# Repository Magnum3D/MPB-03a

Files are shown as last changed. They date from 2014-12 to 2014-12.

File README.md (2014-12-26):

MPB-03a
===========
Reprap Electronics for Magnum printers based on Printrboard

Отличия платы:

1. Плата питается напряжением 24 вольта (стол, экструдер и двигатели)
2. Установлен ЦАП для регулировки тока двигателей командами G-кода (как в версии F и исправлены ошибки).
3. Для питания вентиляторов добавлен дополнительный импульсный преобразователь на 12 вольт
4. Добавлено 4 мосфета с обвязкой - 2 для вентиляторов и 2 для светодиодных лент.
5. Заменены разъемы питания и нагревательного стола на мощные разъемы Molex.
6. Добавлен внешний разъем DSUB и на него выведено питание, ножки процессора и шина I2C
7. Мелкие исправления, доработки.

Постоянно ведется работа над усовершенствованием и доработкой платы, поэтому версия установленная в конкретный эксземпляр принтера может незначительно отличаться.

For more info see the Reprap wiki page http://reprap.org/wiki/Printrboard

The BoM with Digikey P/N's is available here: http://goo.gl/hQNEm

This project, and all of its design files (including the layout), is licensed under the [Creative Commons Attribution-ShareAlike 3.0 Unported](http://creativecommons.org/licenses/by-sa/3.0/) license.

Anyone found to be in violation of this license may not produce or discribute any products using these designs, and will have legal action taken against them.

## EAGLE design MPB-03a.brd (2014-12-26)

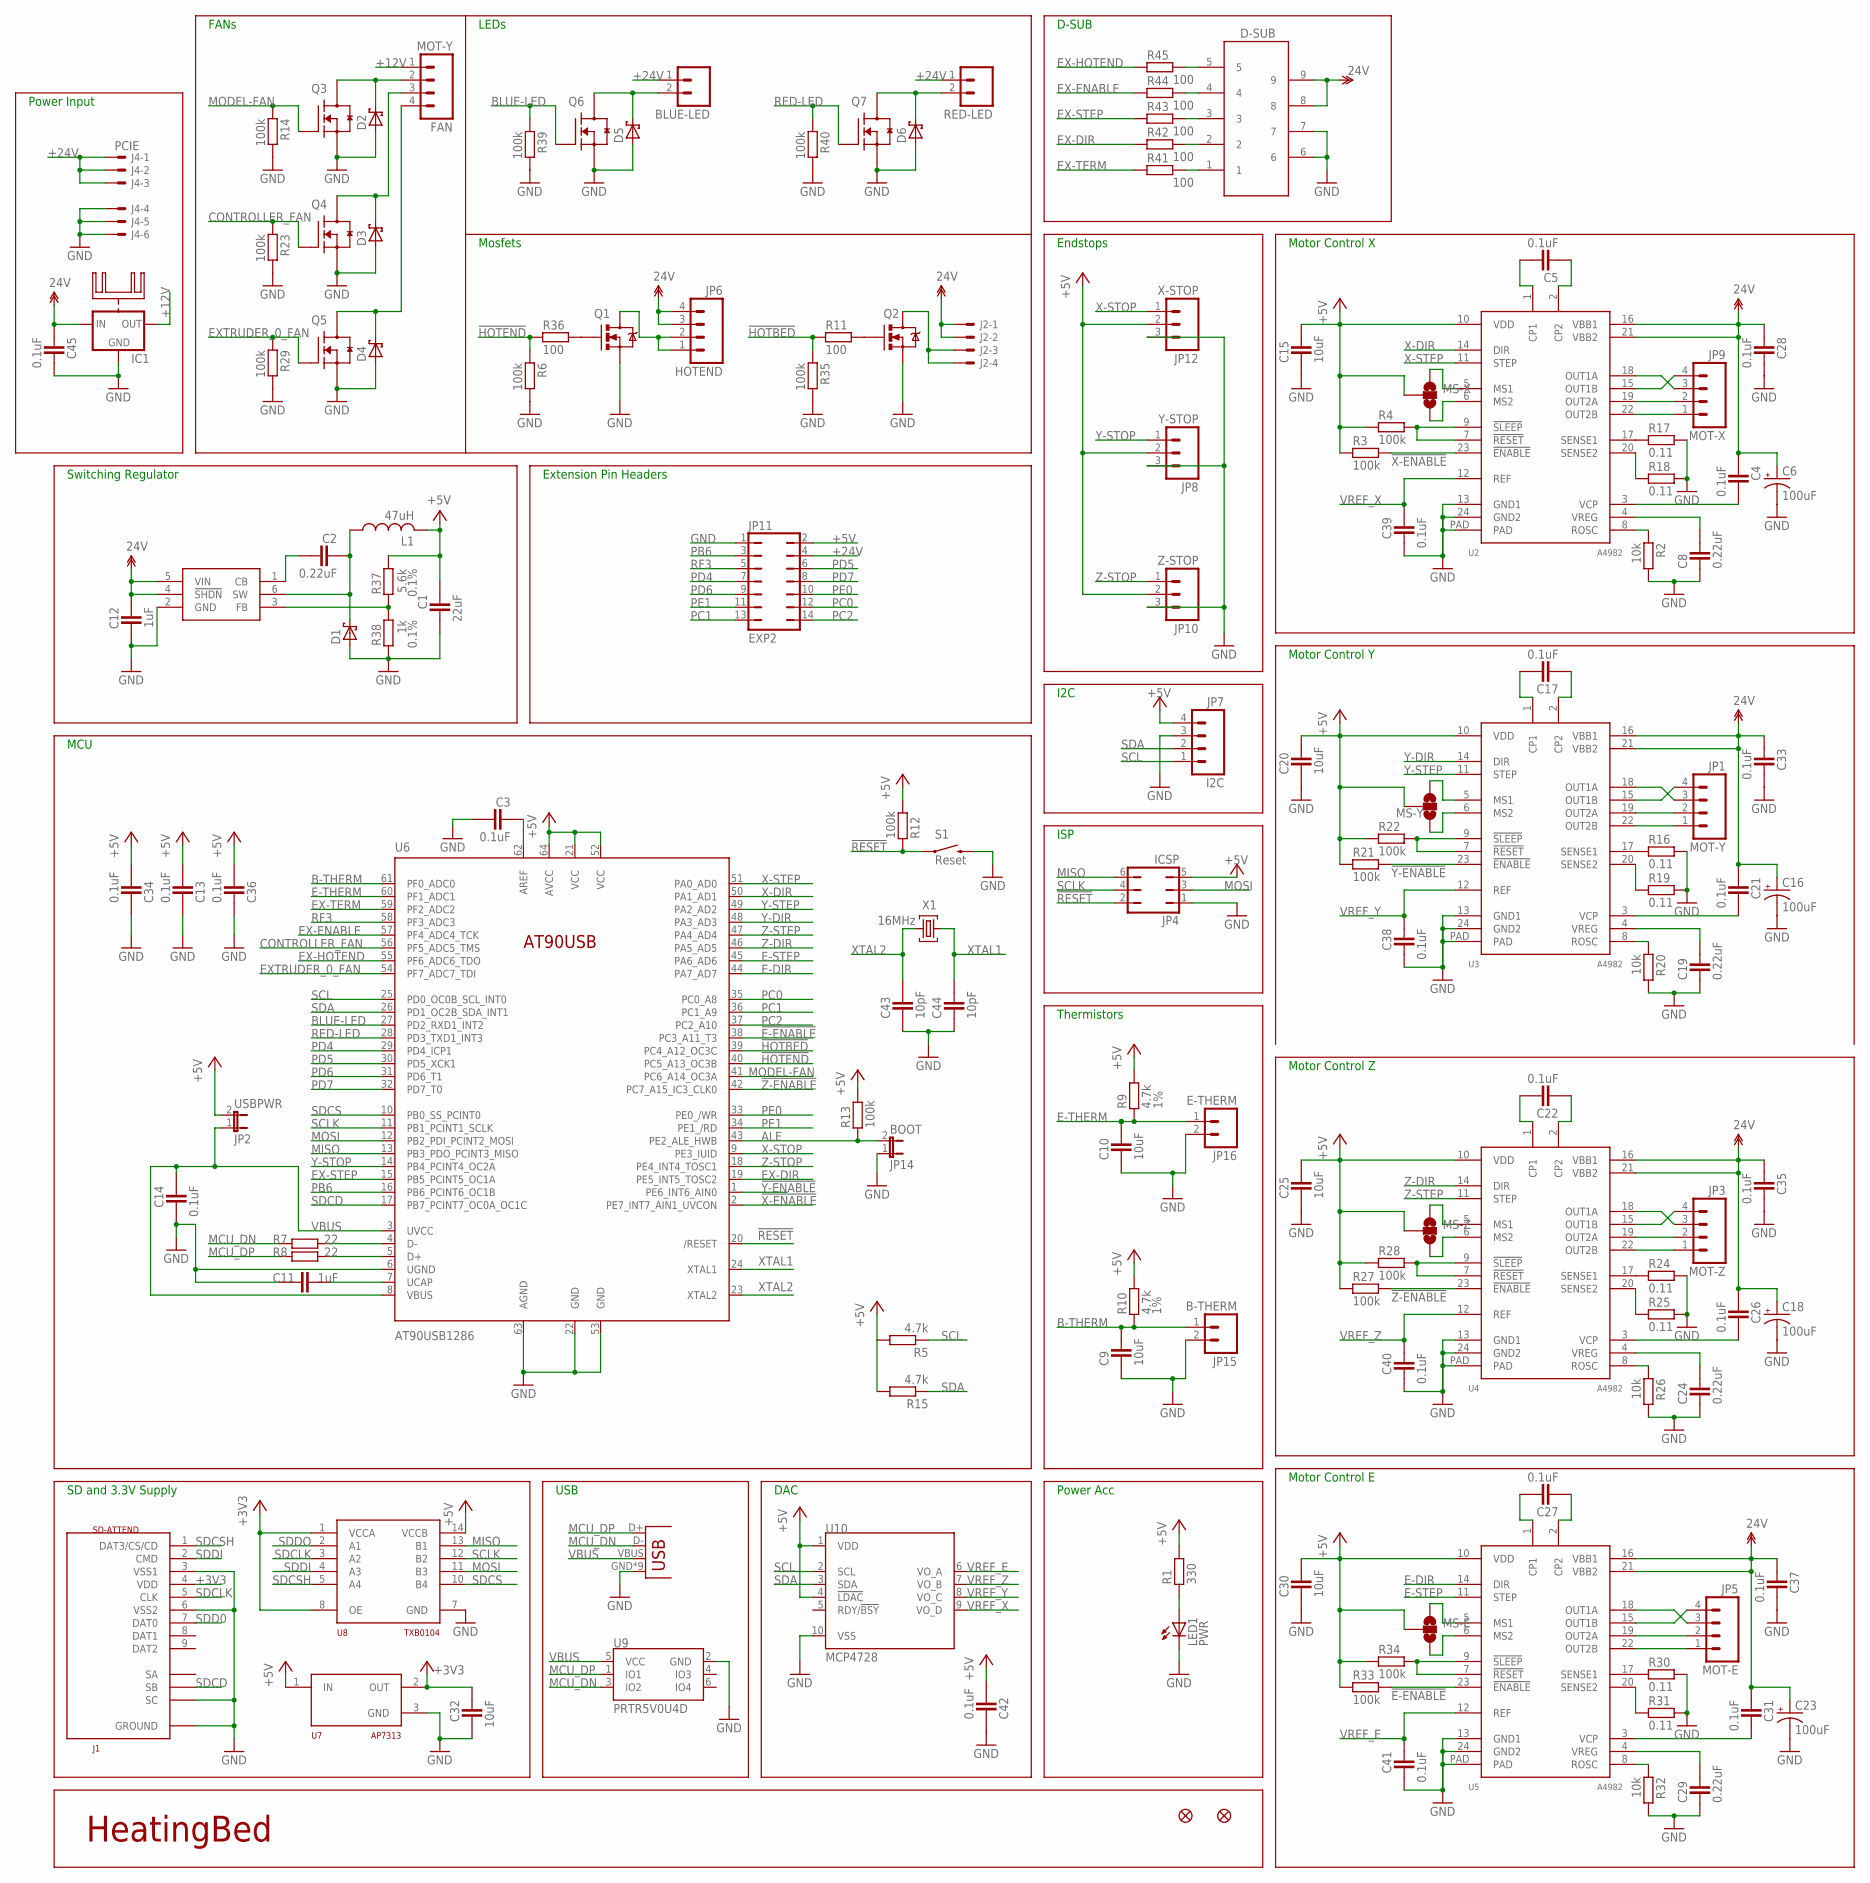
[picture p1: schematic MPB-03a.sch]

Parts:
BLUE-LED: M02POLAR; MOLEX-1X2
C1: 22uF; CAPC2012X145AN
C2, C8, C19, C24, C29: 0.22uF; CAPC2012X145AN
C3, C4, C5, C13, C14, C17, C21, C22, C26, C27, C28, C31, C33, C34, C35, C36, C37, C38, C39, C40, C41, C42, C45: 0.1uF; CAPC2012X145AN
C6, C16, C18, C23: 100uF; PANASONIC_D
C9, C10, C15, C20, C25, C30, C32: 10uF; CAPC2012X145AN
C11, C12: 1uF; CAPC2012X145AN
C43, C44: 10pF; CAPC2012X145AN
D1, D2, D3, D4, D5, D6: SCH-DIODESMA; SMA
D-SUB: 618009211721
FAN: MOT-Y; MOLEX-1X4
IC1: 78XXH; TO220-15X17X25
J1: SD-ATTEND
J2: 5566-4
J3: USB-MICRO-PTH; USB-MICROB-PTH
J4: PCIE; 5566-6
JP1: MOT-Y; MOLEX-1X4
JP2: USBPWR; 1X02
JP3: MOT-Z; MOLEX-1X4
JP4: ICSP; JP3Q
JP5: MOT-E; MOLEX-1X4
JP6: HOTEND; MOLEX-1X4
JP7: I2C; MOLEX-1X4
JP8: Y-STOP; MOLEX-1X3
JP9: MOT-X; MOLEX-1X4
JP10: Z-STOP; MOLEX-1X3
JP11: EXP2; JP7Q
JP12: X-STOP; MOLEX-1X3
JP14: BOOT; 1X02
JP15: B-THERM; 1X02
JP16: E-THERM; 1X02
JP26, JP33: FIDUCIAL1X2.5; FIDUCIAL-1X2.5
L1: 47uH; SDR1006
LED1: PWR; CHIP-LED0805
MS-E: SOLDERJUMPER_2WAYCONNECTED; SJ_3_CONNECTED
MS-X: SOLDERJUMPER_2WAYCONNECTED; SJ_3_CONNECTED
MS-Y: SOLDERJUMPER_2WAYCONNECTED; SJ_3_CONNECTED
MS-Z: SOLDERJUMPER_2WAYCONNECTED; SJ_3_CONNECTED
Q1, Q2: RFP30N06LE; TO220V
Q3, Q4, Q5, Q6, Q7: RFP30N06LE; SOT95P280X135-3N
R1: 330; RESC2012X70N
R2, R20, R26, R32: 10k; RESC2012X70N
R3, R4, R6, R12, R13, R14, R21, R22, R23, R27, R28, R29, R33, R34, R35, R39, R40: 100k; RESC2012X70N
R5, R15: 4.7k; RESC2012X70N
R7, R8: 22; RESC2012X70N
R9, R10: 4.7k; RESC2012X70N; TOLERANCE 1%
R11, R36, R41, R42, R43, R44, R45: 100; RESC2012X70N
R16, R17, R18, R19, R24, R25, R30, R31: 0.11; RESC2012X70N
R37: 5.6k; RESC2012X70N; TOLERANCE 0.1%
R38: 1k; RESC2012X70N; TOLERANCE 0.1%
RED-LED: M02POLAR; MOLEX-1X2
S1: Reset; TACTILE_SWITCH_TALL
U1: LM2841; TSOT6
U2, U3, U4, U5: A4982; TSSOP-24
U6: AT90USB1286; TQFP64-2
U7: AP7313; SOT23C
U8: TXB0104; TSSOP14
U9: PRTR5V0U4D; SOT23-6
U10: MCP4728; MSOP10
X1: 16MHz; NDK-XTAL

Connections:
!E-ENABLE: R33.2, U5.23 (!ENABLE), U6.38 (PC3_A11_T3)
!HOTBED: R11.1, R35.1, U6.39 (PC4_A12_OC3C)
!HOTEND: R6.1, R36.1, U6.40 (PC5_A13_OC3B)
!RESET: JP4.2, R12.1, S1.A2 (1), U6.20 (/RESET)
!X-ENABLE: R3.2, U2.23 (!ENABLE), U6.2 (PE7_INT7_AIN1_UVCON)
!Y-ENABLE: R21.2, U3.23 (!ENABLE), U6.1 (PE6_INT6_AIN0)
!Z-ENABLE: R27.2, U4.23 (!ENABLE), U6.42 (PC7_A15_IC3_CLK0)
+3V3: C32.1, J1.4 (VDD), U7.2 (OUT), U8.1 (VCCA), U8.8 (OE)
+5V: C1.1, C13.2, C15.2, C20.2, C25.2, C30.2, C34.2, C36.2, C42.2, JP2.2, JP4.5, JP7.4, JP8.2, JP10.2, JP11.2, JP12.2, L1.P$2 (2), MS-E.2, MS-X.2, MS-Y.2, MS-Z.2, R1.2, R3.1, R4.1, R5.2, R9.2, R10.2, R12.2, R13.2, R15.2, R21.1, R22.1, R27.1, R28.1, R33.1, R34.1, R37.1, U2.10 (VDD), U3.10 (VDD), U4.10 (VDD), U5.10 (VDD), U6.21 (VCC), U6.52 (VCC), U6.64 (AVCC), U7.1 (IN), U8.14 (VCCB), U10.1 (VDD), U10.4 (!LDAC)
+12V: FAN.1, IC1.OUT
+24V: BLUE-LED.1, C4.1, C6.+, C12.1, C16.+, C18.+, C21.1, C23.+, C26.1, C28.1, C31.1, C33.1, C35.1, C37.1, C45.1, D-SUB.8, D-SUB.9, IC1.IN, J2.1, J2.2, J4.1, J4.2, J4.3, JP6.3, JP6.4, JP11.4, RED-LED.1, U1.4 (!SHDN), U1.5 (VIN), U2.16 (VBB1), U2.21 (VBB2), U3.16 (VBB1), U3.21 (VBB2), U4.16 (VBB1), U4.21 (VBB2), U5.16 (VBB1), U5.21 (VBB2)
ALE: JP14.2, R13.1, U6.43 (PE2_ALE_HWB)
AREF: C3.1, U6.62 (AREF)
B-THERM: C9.2, JP15.1, R10.1, U6.61 (PF0_ADC0)
BLUE-LED: Q6.1 (G), R39.1, U6.27 (PD2_RXD1_INT2)
CONTROLLER_FAN: Q4.1 (G), R23.1, U6.56 (PF5_ADC5_TMS)
E-DIR: U5.14 (DIR), U6.44 (PA7_AD7)
E-STEP: U5.11 (STEP), U6.45 (PA6_AD6)
E-THERM: C10.2, JP16.1, R9.1, U6.60 (PF1_ADC1)
EX-DIR: R42.1, U6.19 (PE5_INT5_TOSC2)
EX-ENABLE: R44.1, U6.57 (PF4_ADC4_TCK)
EX-HOTEND: R45.1, U6.55 (PF6_ADC6_TDO)
EX-STEP: R43.1, U6.15 (PB5_PCINT5_OC1A)
EX-TERM: R41.1, U6.59 (PF2_ADC2)
EXTRUDER_0_FAN: Q5.1 (G), R29.1, U6.54 (PF7_ADC7_TDI)
GND: C1.2, C3.2, C6.-, C8.1, C9.1, C10.1, C11.1, C12.2, C13.1, C14.2, C15.1, C16.-, C18.-, C19.1, C20.1, C23.-, C24.1, C25.1, C28.2, C29.1, C30.1, C32.2, C33.2, C34.1, C35.2, C36.1, C37.2, C38.2, C39.2, C40.2, C41.2, C42.1, C43.1, C44.1, C45.2, D1.A, D2.A, D3.A, D4.A, D5.A, D6.A, D-SUB.6, D-SUB.7, IC1.GND, J1.3 (VSS1), J1.6 (VSS2), J1.G (GROUND), J1.SC, J3.GND, J3.GND1 (GND), J3.GND2 (GND), J3.GND3 (GND), J3.GND4 (GND), J3.GND5 (GND), J3.GND6 (GND), J3.GND7 (GND), J3.GND8 (GND), J4.4, J4.5, J4.6, JP4.1, JP7.3, JP8.3, JP10.3, JP11.1, JP12.3, JP14.1, JP15.2, JP16.2, LED1.C, Q1.3 (S), Q2.3 (S), Q3.2 (S), Q4.2 (S), Q5.2 (S), Q6.2 (S), Q7.2 (S), R2.2, R6.2, R14.2, R16.2, R17.2, R18.2, R19.2, R20.2, R23.2, R24.2, R25.2, R26.2, R29.2, R30.2, R31.2, R32.2, R35.2, R38.2, R39.2, R40.2, S1.B2 (2), U1.2 (GND), U2.13 (GND1), U2.24 (GND2), U2.PAD, U3.13 (GND1), U3.24 (GND2), U3.PAD, U4.13 (GND1), U4.24 (GND2), U4.PAD, U5.13 (GND1), U5.24 (GND2), U5.PAD, U6.6 (UGND), U6.22 (GND), U6.53 (GND), U6.63 (AGND), U7.3 (GND), U8.7 (GND), U9.2 (GND), U10.10 (VSS)
HOTBED-GND: J2.3, J2.4, Q2.2 (D)
HOTEND-GND: JP6.1, JP6.2, Q1.2 (D)
MCU_DN: J3.D-, R7.1, U9.3 (IO2)
MCU_DP: J3.D+, R8.1, U9.1 (IO1)
MISO: JP4.6, U6.13 (PB3_PDO_PCINT3_MISO), U8.13 (B1)
MODEL-FAN: Q3.1 (G), R14.1, U6.41 (PC6_A14_OC3A)
MOSI: JP4.3, U6.12 (PB2_PDI_PCINT2_MOSI), U8.11 (B3)
unnamed: LED1.A, R1.1
unnamed: D2.C, FAN.2, Q3.3 (D)
unnamed: R7.2, U6.4 (D-)
unnamed: R8.2, U6.5 (D+)
unnamed: D3.C, FAN.3, Q4.3 (D)
unnamed: D4.C, FAN.4, Q5.3 (D)
unnamed: Q2.1 (G), R11.2
unnamed: BLUE-LED.2, D5.C, Q6.3 (D)
unnamed: C11.2, U6.7 (UCAP)
unnamed: JP9.3, U2.18 (OUT1A)
unnamed: C5.2, U2.1 (CP1)
unnamed: C5.1, U2.2 (CP2)
unnamed: R2.1, U2.8 (ROSC)
unnamed: R17.1, U2.17 (SENSE1)
unnamed: R18.1, U2.20 (SENSE2)
unnamed: C4.2, U2.3 (VCP)
unnamed: JP9.4, U2.15 (OUT1B)
unnamed: D-SUB.5, R45.2
unnamed: C8.2, U2.4 (VREG)
unnamed: JP9.2, U2.19 (OUT2A)
unnamed: R4.2, U2.7 (!RESET), U2.9 (!SLEEP)
unnamed: R37.2, R38.1, U1.3 (FB)
unnamed: JP9.1, U2.22 (OUT2B)
unnamed: JP1.2, U3.19 (OUT2A)
unnamed: JP1.1, U3.22 (OUT2B)
unnamed: JP1.4, U3.15 (OUT1B)
unnamed: MS-X.1, U2.5 (MS1)
unnamed: MS-X.3, U2.6 (MS2)
unnamed: C17.2, U3.1 (CP1)
unnamed: C17.1, U3.2 (CP2)
unnamed: JP1.3, U3.18 (OUT1A)
unnamed: R19.1, U3.20 (SENSE2)
unnamed: D6.C, Q7.3 (D), RED-LED.2
unnamed: R20.1, U3.8 (ROSC)
unnamed: C19.2, U3.4 (VREG)
unnamed: R22.2, U3.7 (!RESET), U3.9 (!SLEEP)
unnamed: C21.2, U3.3 (VCP)
unnamed: R16.1, U3.17 (SENSE1)
unnamed: JP3.4, U4.15 (OUT1B)
unnamed: JP3.3, U4.18 (OUT1A)
unnamed: JP3.2, U4.19 (OUT2A)
unnamed: MS-Y.1, U3.5 (MS1)
unnamed: MS-Y.3, U3.6 (MS2)
unnamed: C22.2, U4.1 (CP1)
unnamed: C22.1, U4.2 (CP2)
unnamed: R24.1, U4.17 (SENSE1)
unnamed: R25.1, U4.20 (SENSE2)
unnamed: R26.1, U4.8 (ROSC)
unnamed: C24.2, U4.4 (VREG)
unnamed: R28.2, U4.7 (!RESET), U4.9 (!SLEEP)
unnamed: C26.2, U4.3 (VCP)
unnamed: JP3.1, U4.22 (OUT2B)
unnamed: JP5.4, U5.15 (OUT1B)
unnamed: JP5.3, U5.18 (OUT1A)
unnamed: JP5.2, U5.19 (OUT2A)
unnamed: MS-Z.1, U4.5 (MS1)
unnamed: MS-Z.3, U4.6 (MS2)
unnamed: C27.2, U5.1 (CP1)
unnamed: C27.1, U5.2 (CP2)
unnamed: R30.1, U5.17 (SENSE1)
unnamed: R31.1, U5.20 (SENSE2)
unnamed: D-SUB.4, R44.2
unnamed: R32.1, U5.8 (ROSC)
unnamed: C29.2, U5.4 (VREG)
unnamed: R34.2, U5.7 (!RESET), U5.9 (!SLEEP)
unnamed: C31.2, U5.3 (VCP)
unnamed: JP5.1, U5.22 (OUT2B)
unnamed: D-SUB.3, R43.2
unnamed: D-SUB.2, R42.2
unnamed: Q1.1 (G), R36.2
unnamed: MS-E.1, U5.5 (MS1)
unnamed: MS-E.3, U5.6 (MS2)
unnamed: D-SUB.1, R41.2
unnamed: C2.1, D1.C, L1.P$1 (1), U1.6 (SW)
unnamed: C2.2, U1.1 (CB)
PB6: JP11.3, U6.16 (PB6_PCINT6_OC1B)
PC0: JP11.12, U6.35 (PC0_A8)
PC1: JP11.13, U6.36 (PC1_A9)
PC2: JP11.14, U6.37 (PC2_A10)
PD4: JP11.7, U6.29 (PD4_ICP1)
PD5: JP11.6, U6.30 (PD5_XCK1)
PD6: JP11.9, U6.31 (PD6_T1)
PD7: JP11.8, U6.32 (PD7_T0)
PE0: JP11.10, U6.33 (PE0_/WR)
PE1: JP11.11, U6.34 (PE1_/RD)
RED-LED: Q7.1 (G), R40.1, U6.28 (PD3_TXD1_INT3)
RF3: JP11.5, U6.58 (PF3_ADC3)
SCL: JP7.1, R5.1, U6.25 (PD0_OC0B_SCL_INT0), U10.2 (SCL)
SCLK: JP4.4, U6.11 (PB1_PCINT1_SCLK), U8.12 (B2)
SDA: JP7.2, R15.1, U6.26 (PD1_OC2B_SDA_INT1), U10.3 (SDA)
SDCD: J1.SB, U6.17 (PB7_PCINT7_OC0A_OC1C)
SDCLK: J1.5 (CLK), U8.3 (A2)
SDCS: U6.10 (PB0_SS_PCINT0), U8.10 (B4)
SDCSH: J1.1 (DAT3/CS/CD), U8.5 (A4)
SDD0: J1.7 (DAT0)
SDDI: J1.2 (CMD), U8.4 (A3)
SDDO: U8.2 (A1)
VBUS: C14.1, J3.VBUS, JP2.1, U6.3 (UVCC), U6.8 (VBUS), U9.5 (VCC)
VREF_E: C41.1, U5.12 (REF), U10.6 (VO_A)
VREF_X: C39.1, U2.12 (REF), U10.9 (VO_D)
VREF_Y: C38.1, U3.12 (REF), U10.8 (VO_C)
VREF_Z: C40.1, U4.12 (REF), U10.7 (VO_B)
X-DIR: U2.14 (DIR), U6.50 (PA1_AD1)
X-STEP: U2.11 (STEP), U6.51 (PA0_AD0)
X-STOP: JP12.1, U6.9 (PE3_IUID)
XTAL1: C44.2, U6.24 (XTAL1), X1.P$1 (1)
XTAL2: C43.2, U6.23 (XTAL2), X1.P$2 (2)
Y-DIR: U3.14 (DIR), U6.48 (PA3_AD3)
Y-STEP: U3.11 (STEP), U6.49 (PA2_AD2)
Y-STOP: JP8.1, U6.14 (PB4_PCINT4_OC2A)
Z-DIR: U4.14 (DIR), U6.46 (PA5_AD5)
Z-STEP: U4.11 (STEP), U6.47 (PA4_AD4)
Z-STOP: JP10.1, U6.18 (PE4_INT4_TOSC1)

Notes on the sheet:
Motor Control X
Motor Control Y
Motor Control Z
Motor Control E
ISP
Thermistors
Endstops
Mosfets
Power Acc
HeatingBed
Extension Pin Headers
Switching Regulator
SD and 3.3V Supply
Power Input
MCU
I2C
USB
DAC
FANs
LEDs
D-SUB

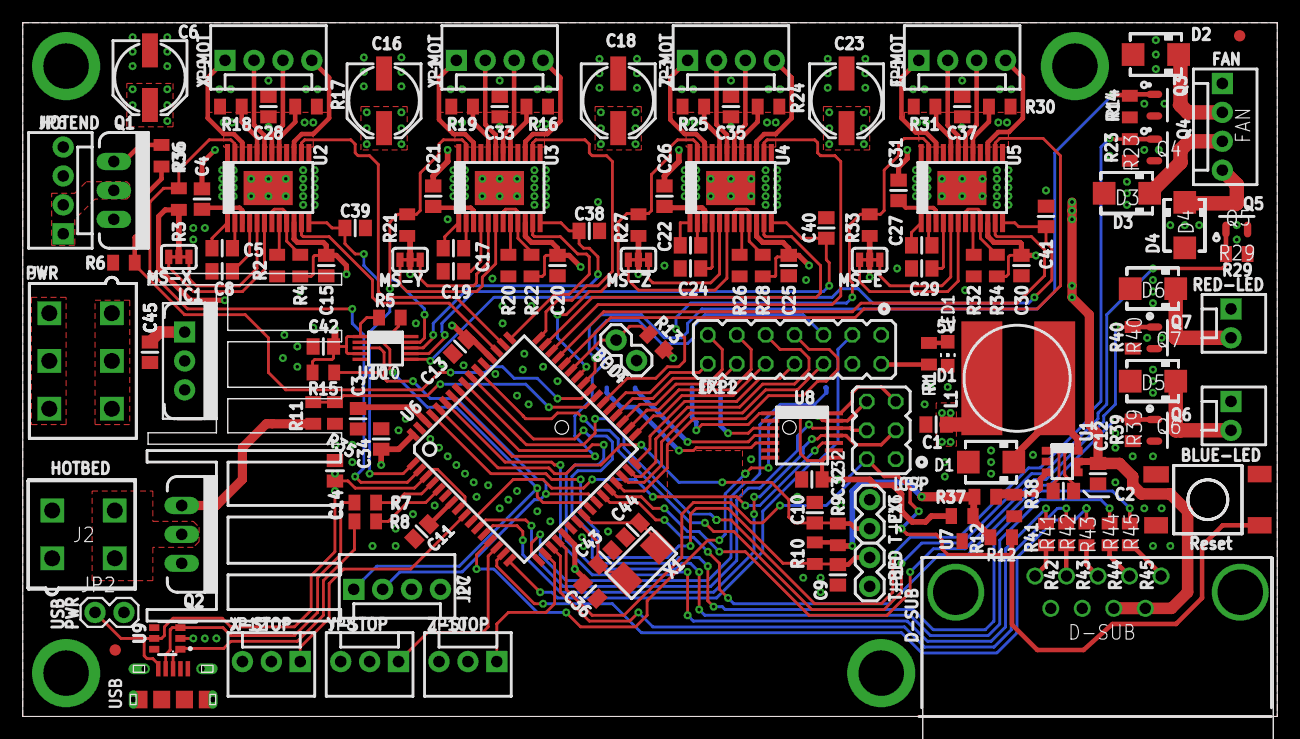
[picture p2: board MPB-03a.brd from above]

Board: 4 copper layers, 110.2 x 61.0 mm, 146 parts (1 on the bottom side), 144 nets.

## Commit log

2014-12-26 Добавлены исходные файлы проекта.
    [MPB-03a.brd, MPB-03a.sch]
2014-12-26 Обновлено описание платы.

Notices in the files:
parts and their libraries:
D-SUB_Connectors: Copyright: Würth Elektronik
